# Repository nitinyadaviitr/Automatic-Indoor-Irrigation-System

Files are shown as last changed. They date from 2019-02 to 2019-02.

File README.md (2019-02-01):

# Indoor-Irrigation-System

# Abstract
Our motivation to build this bot is to preserve our green earth and save water by changing the conventional way of plantation.  

# Team Members
<ul>
<li ><a href="https://www.facebook.com/people/Nitin-Yadav/100002014363690">Nitin Yadav</a></li>
<li><a href="https://www.facebook.com/utkarshdeepak23">Utkarsh Deepak</a></li>
<li><a href="https://www.facebook.com/tathagat.chaurasiya">Tathagat Chaurasiya</a></li>
<li><a href="https://www.facebook.com/profile.php?id=100004414771823">Ashish Kumar</a></li>
<li><a href="">Abhishek Mishra</a></li>
<li><a href="https://www.facebook.com/profile.php?id=100011648292342">Rahul Yadav</a></li>
</ul>

# Mentors
<ul>
<li><a href="https://www.facebook.com/profile.php?id=100003364416121">Mohit Gupta</a></li>
<li><a href="https://www.facebook.com/prasants021">Prashant Shekhar Singh</a></li>
<li><a href="https://www.facebook.com/clickonshivam">Shivam Parashar</a></li>
<li><a href="https://www.facebook.com/pritam6505">Pritam Kumar</a></li>
<li><a href="https://www.facebook.com/pankajmindfreak">Pankaj Kumar Singh</a></li>
</ul>

# Pre-Requisites
 
 <b>Hardware:</b>
<ol>
<li>Arduino UNO</li>
<li>2	Motor Driver L298N</li>
<li>12V Solenoidal Value</li>
<li>1 Servo motor MG995</li>
<li>3 High Torque Stepper Motors</li>
<li>ULN2003</li>
<li>12V DC Power Adapter</li>
<li>Relimates</li>
<li>Jumper Wires</li>
<li>LM317T Voltage Divider</li>
<li>Resistors</li>
<li>Breadboard</li>
<li>DST</li>
<li>15cm and 50cm Slider</li>
<li>Wooden Base (dia.52cm)</li>
<li>Wooden Circular Rim(inner dia. 980mm and outer dia. 1080mm)</li>
<li>5m Square Channel</li>
<li>L Channels</li>
<li>Rack And Pinion</li>
<li>Aluminium Plate</li>
<li>Aluminium Sheet</li>
<li>Hollow Circular Rod</li>
<li>Motor Mount</li>
<li>Some 3d printed Parts</li> 
</ol>

 <b>Software:</b>
 
•	<a href ="https://www.arduino.cc/en/main/software">Arduino IDE</a>

# D.I.Y. Steps From Scratch
<ol>
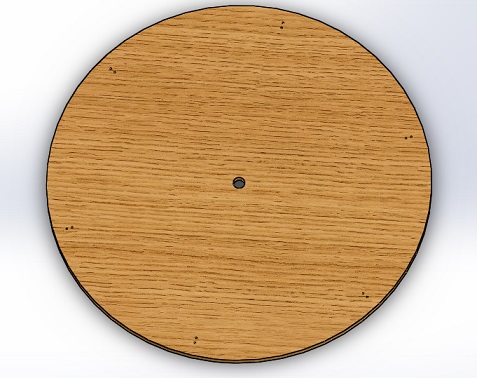
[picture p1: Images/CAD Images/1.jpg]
<li><p>A wooden base of 104cm diameter is chosen as the base for the whole model. A cavity (diameter) is made so that a rod can be placed to support the moving arm.</p></li>
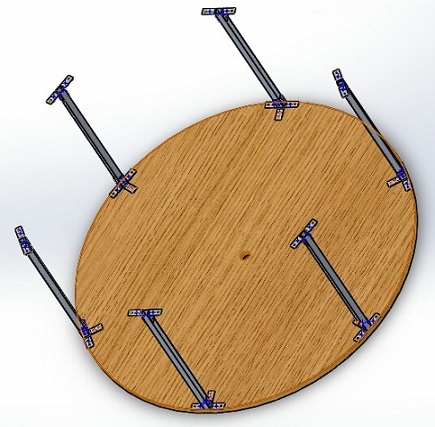
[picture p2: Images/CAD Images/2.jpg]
<li><p>6 square channels of length 50cm are mounted vertically on the wooden base with the help of L-channel to give them a rigid grip on the base. Every square channel has 3 L-channel attached to it on the base and 2 on its top so that the circular rim is fixed firmly and does not move when the arm rotates on it. This is important for a precise movement.</p></li>
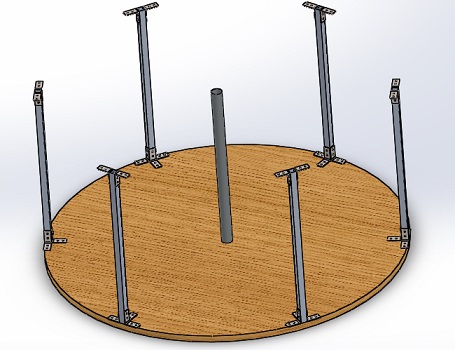
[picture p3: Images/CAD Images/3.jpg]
<li><p>To give support to the moving arm, a rod of 51.4 cm is fixed on the base with a diameter of 3.17cm.</p></li>
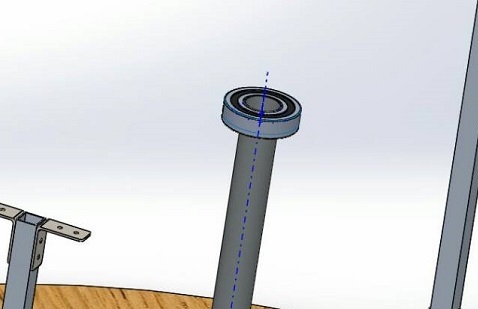
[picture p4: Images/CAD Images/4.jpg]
<li><p>A ball bearing of the same inner diameter as that of the rod is fixed on the rod so that the arm can rotate.</p></li>
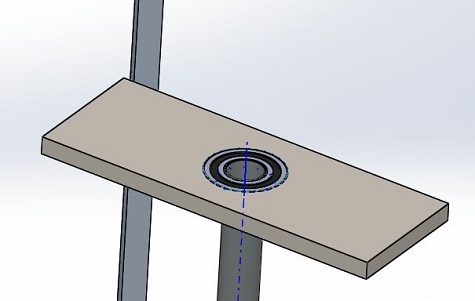
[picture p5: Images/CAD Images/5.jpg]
<li><p>An aluminum plate of about 1cm thickness is used to make a rectangular plate of about 11cm*30 cm, on which, whole of the arm is to be mounted. This aluminum plate has a circular cavity in which the bearing is fitted.</p></li>
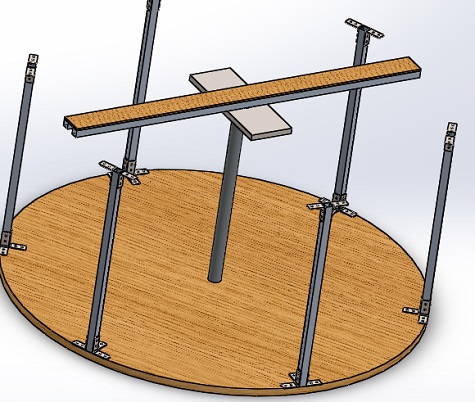
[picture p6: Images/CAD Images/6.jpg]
<li><p>The arm has two square channels of 96cm on which a cardboard sheet is mounted to have a platform for rest of the mechanism.</p></li>
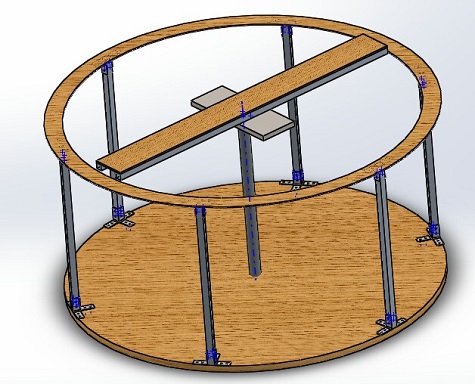
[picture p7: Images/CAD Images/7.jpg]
<li><p>The rim is placed on the vertical square channels and fixed by screwing it to the 2 L-channels.</p></li>
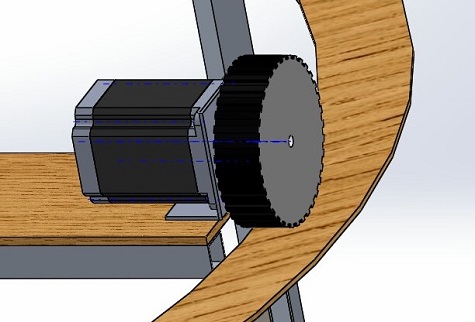
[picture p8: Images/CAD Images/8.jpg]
<li><p>A stepper motor (with a wheel) is fixed at one end of the arm to provide the circular motion to the arm. The motor is mounted on the cardboard sheet with a motor mount.</p></li>
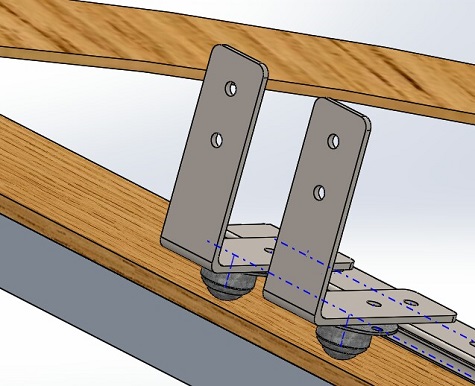
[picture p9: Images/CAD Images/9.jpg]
<li><p>A linear slider of 50cm is screwed on the cardboard sheet for the linear movement of the seeding mechanism. At the end of slider, 2 L-channel are fixed with castor wheels attached at their bottom to provide a smooth movement to the slider despite of the weight of vertical mechanism.</p></li>
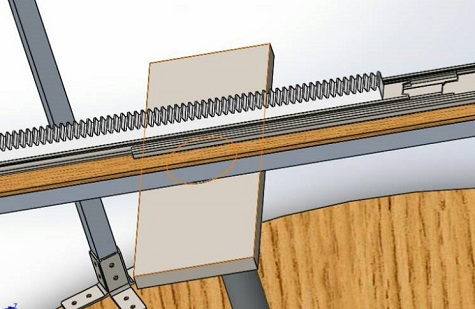
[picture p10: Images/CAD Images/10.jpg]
<li><p>A rack of 40cm is attached on the slider to move it through a stepper motor.</p></li>
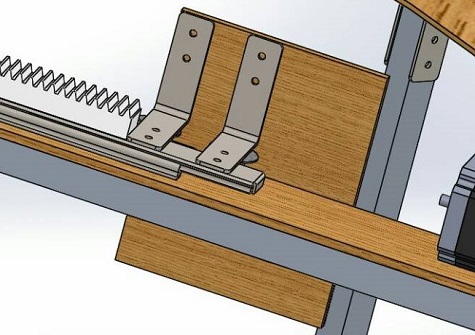
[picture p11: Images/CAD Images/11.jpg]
<li><p>To support the vertical mechanism, a wooden sheet of 15cm*15 cm is used and is fixed on the 2 L-channels with the help of screws.</p></li>
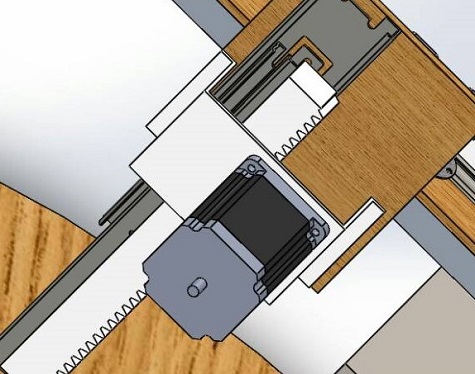
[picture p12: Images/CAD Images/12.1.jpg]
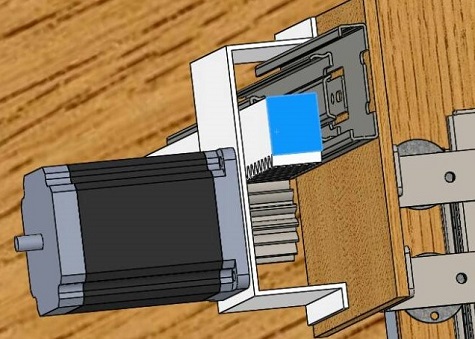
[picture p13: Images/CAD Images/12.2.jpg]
<li><p>In the vertical mechanism, a slider of 15cm is fixed on the wooden sheet and a rack of 25cm is wooden sheet through a u-shaped motor mount (made of ABS/PPS, for 3D printing you can directly access the solid works file provided)</p> </li>
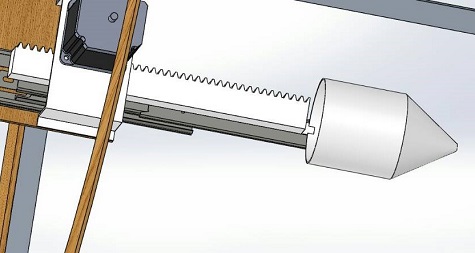
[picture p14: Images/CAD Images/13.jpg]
<li><p>For seeding, a conical flask with a cylindrical top, the seed storage, (made of ABS/PPS) is used in which a servo motor is fixed. The servo motor is used to have a periodic opening and closing of a hole in the storage.</p></li>
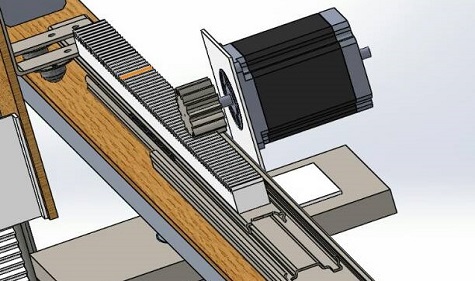
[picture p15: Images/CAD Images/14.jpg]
<li><p>The motor for movement of slider on the horizontal arm is mounted through a motor mount (made of ABS/PPS).</p></li>
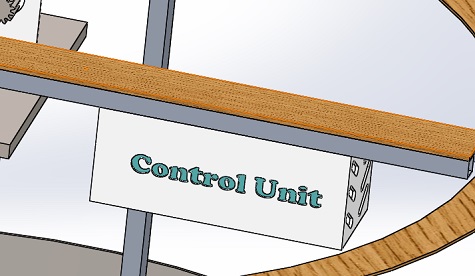
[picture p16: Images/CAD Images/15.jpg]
<li><p>At the vacant side of the arm, whole of the electronic system is mounted. To power the model, the adapter wire is passed through the middle rod. </p></li>
<li>On the aluminum plate in the middle, opposite to the stepper motor, a solenoidal valve is fixed to control the flow of the water.</li>
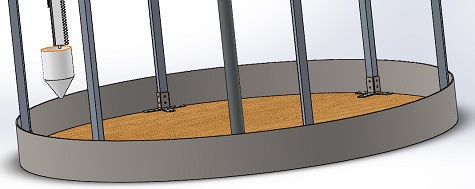
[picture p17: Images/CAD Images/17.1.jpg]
<li><p>Boundary of metal sheet is made to support soil.</p></li>
<li>The water is provided through a container at a certain height higher than the arm to the solenoidal valve.</li>
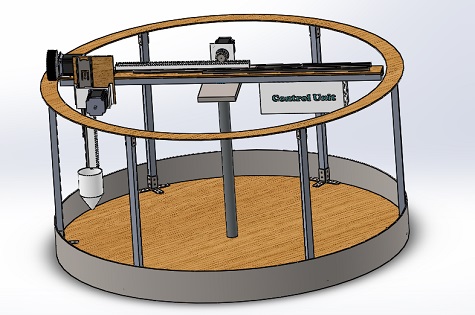
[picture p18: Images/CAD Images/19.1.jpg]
<li><p>After the whole model is made, the whole weight is about 23-25 kg.</p></li>
</ol>

# Instruction on using source code
 Our overall code consists of three sub files. One of them is the <a href="https://github.com/marsiitr/Indoor-Irrigation-System/blob/master/main_code/main_code.ino">main file</a> and others consists of only functions or methods definitons which are called/used in the main file.All the subfiles have been uploaded in github. First, you have to download them all and put them in a folder that has the same name as that of the main file( In our case, "main_code" is the main file).Once you have done this and connected the hardware properly, then you just have to upload the main file to the arduino board and you are ready to go.
# Photos
<div>
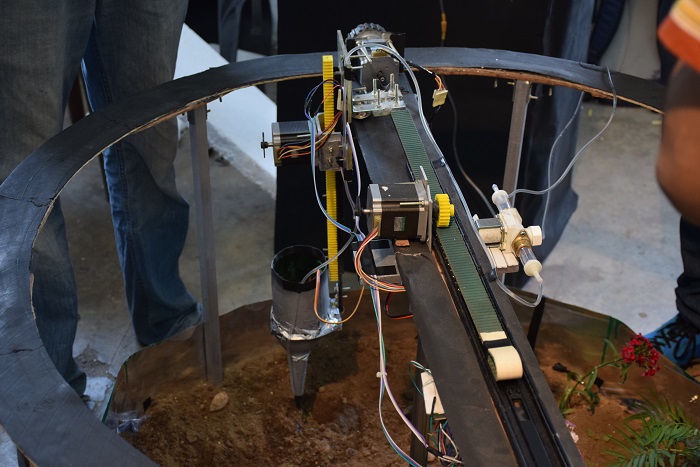
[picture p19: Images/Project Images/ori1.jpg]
<br/>
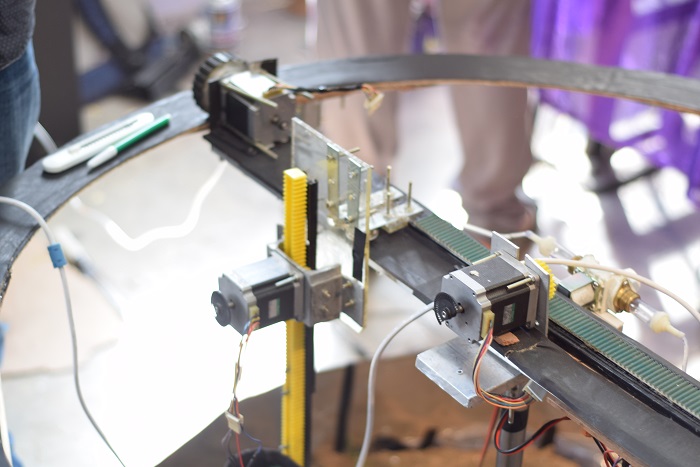
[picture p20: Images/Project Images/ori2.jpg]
<br/>
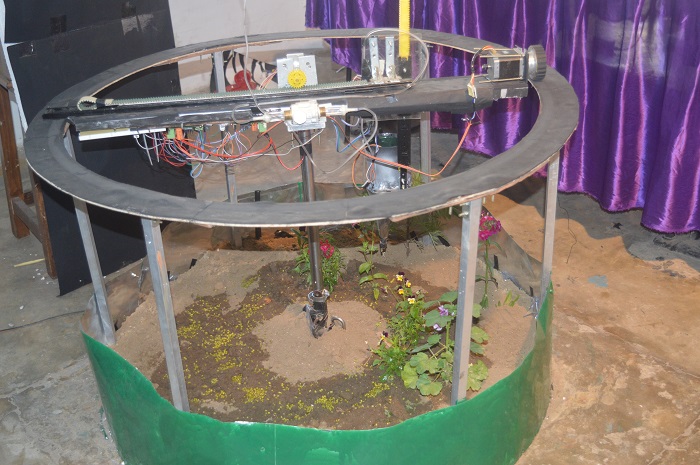
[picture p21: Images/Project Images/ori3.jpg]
<br/>
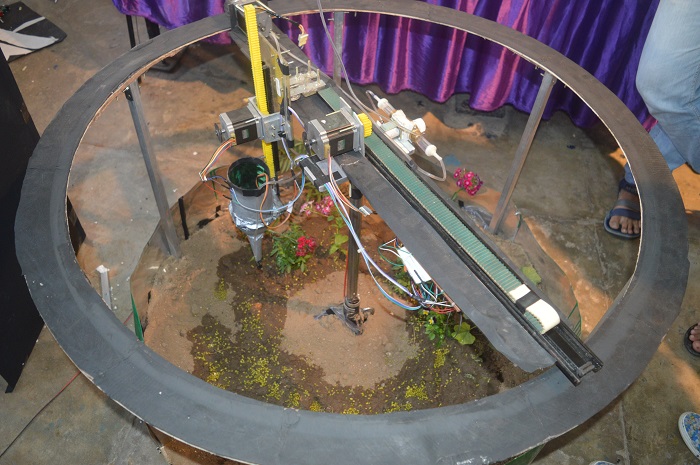
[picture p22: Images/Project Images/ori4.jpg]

</div>

# Results  
1. The mechanism used in the Bot is very effective in saving water and using it efficiently both position and time-wise.
2. The seed bowing mechanism gives us a platform to use the space on the used patch of land efficiently. It can used to accurately place the seed in the position we want to and that is needed to.
3. The energy requirements of the Bot is very low and can be used for long-time with low electricity requirements.
4. The bot has very low heat radiation and thus can be used with continuous working for long time-span.
5. It helps us to grow the plant with proper use of water which results in proper growth of the plant.

# Future scope
 1. This bot has a very good scope in future for people who are not able to give time in gardening but want a patch of land full of   flowers in their backyard. They would require just to spend a few minutes in giving the seeds and water supply to the bot and       rest of the work is automatically done by the bot.
2. For research purposes this bot can be used by researchers to examine the soil quality and its requirements for plantation accurately and without spending much time as most of the work is done by the bot.
3. By farmers to have a proper information about the water and pesticide requirements of soil of their farm so that the growth of grains, vegetables etc. is done with precise information and their growth is properly examined and good quality crops are grown on a larger scale without wastage of water and other resources.

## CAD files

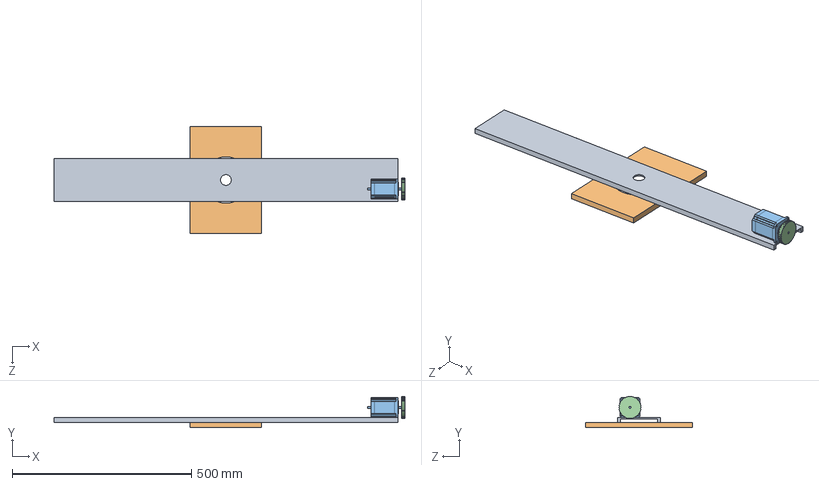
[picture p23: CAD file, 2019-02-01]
Solidworks Assembly/ARM.SLDASM
980.0 x 87.8 x 300.0 mm
arm
holder
step motor

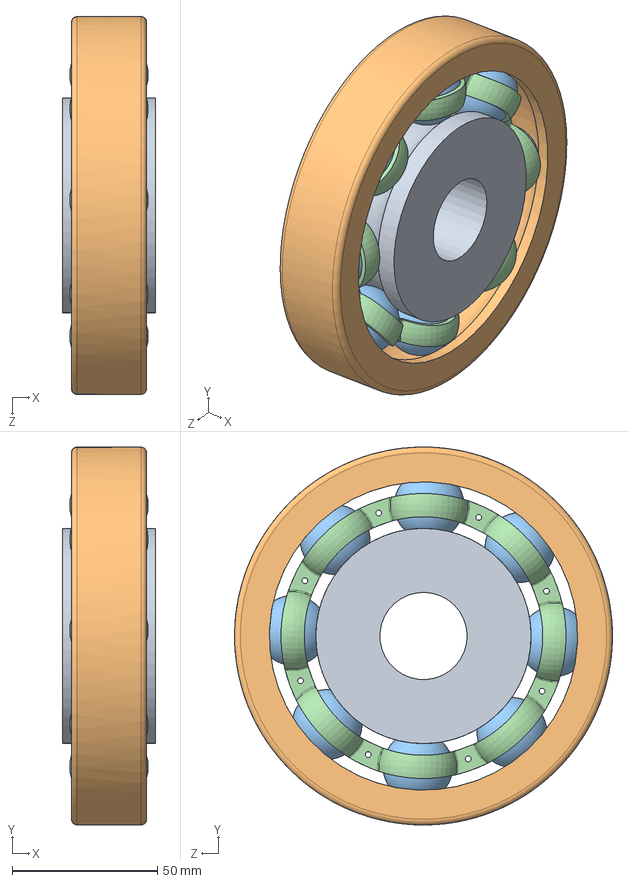
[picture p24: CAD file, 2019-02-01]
Solidworks Assembly/bearing.SLDASM
32.0 x 130.0 x 130.0 mm
hat' x 2

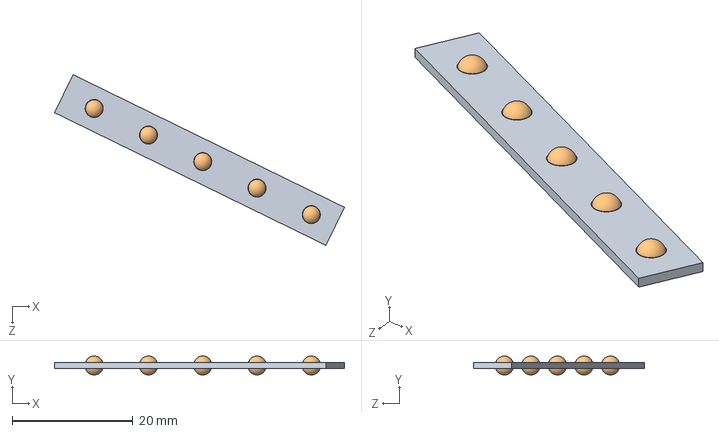
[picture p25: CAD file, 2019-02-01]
Solidworks Assembly/slider 15 cm/MIDDLE SLID WITH BEARING.SLDASM
48.0 x 3.14 x 28.2 mm
middle slit
ball 3 mm x 10

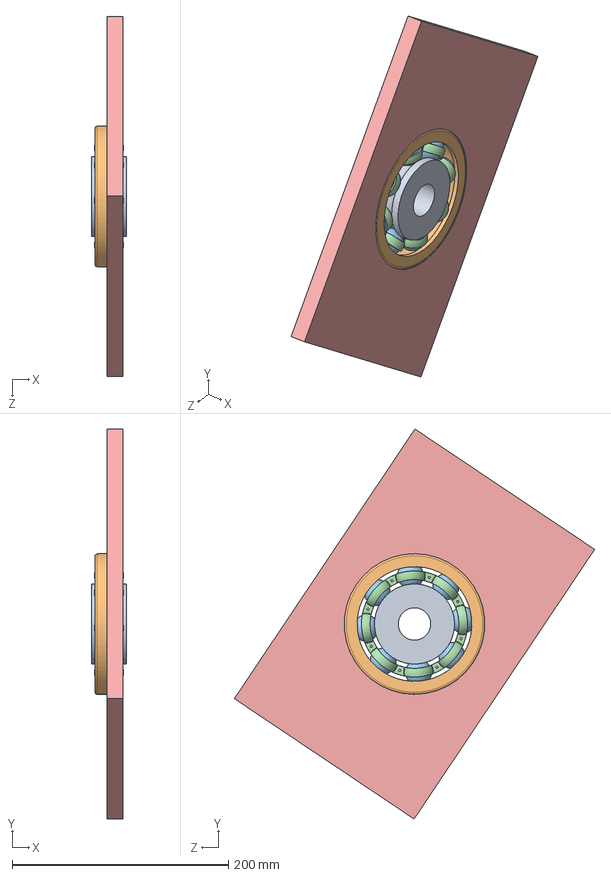
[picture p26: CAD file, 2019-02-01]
Solidworks Assembly/holder1.SLDASM
32.0 x 360.6 x 333.1 mm
hat' x 2
holder

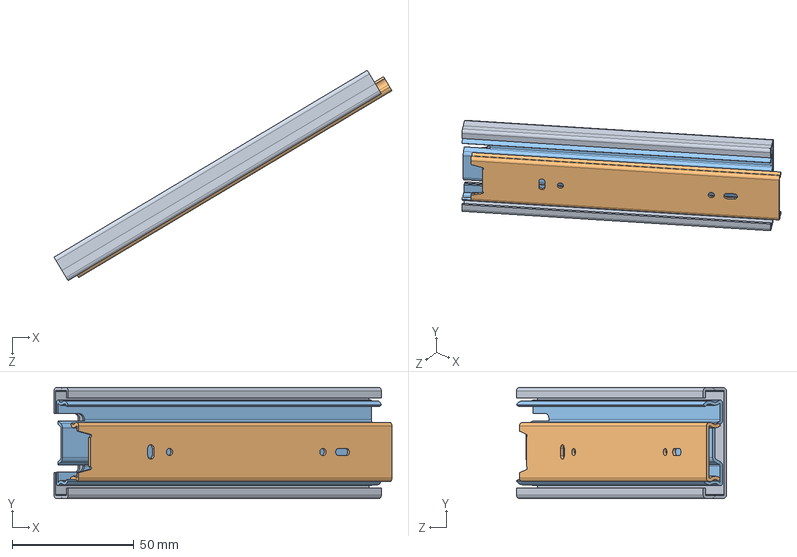
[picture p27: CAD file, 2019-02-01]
Solidworks Assembly/slider 15 cm/final asyy.SLDASM
139.0 x 45.6 x 86.5 mm
base slider final
top slider
Middle slider

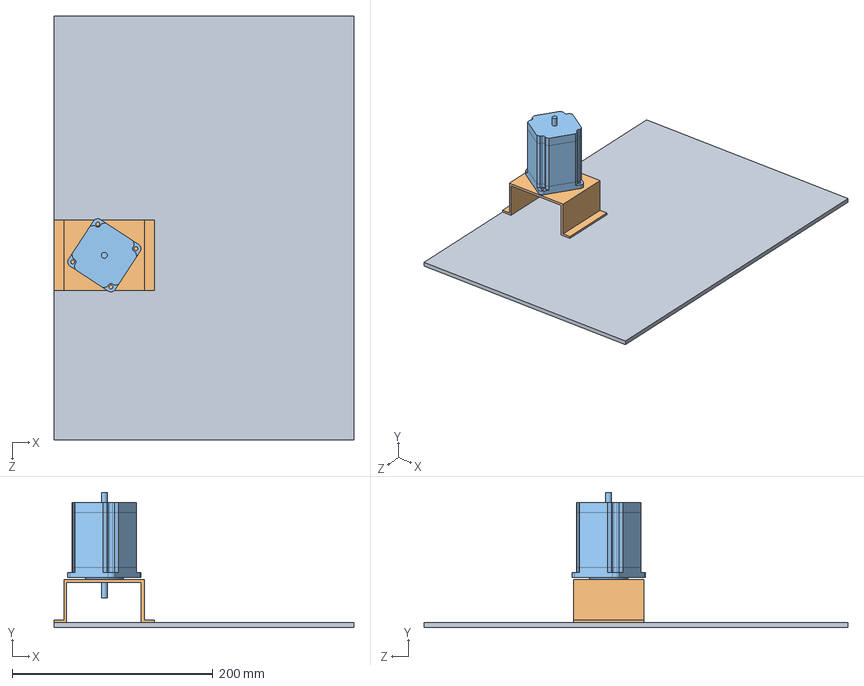
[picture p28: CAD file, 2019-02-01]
Solidworks Assembly/Vertical.SLDASM
298.8 x 134.6 x 422.7 mm
v1
v2
step motor

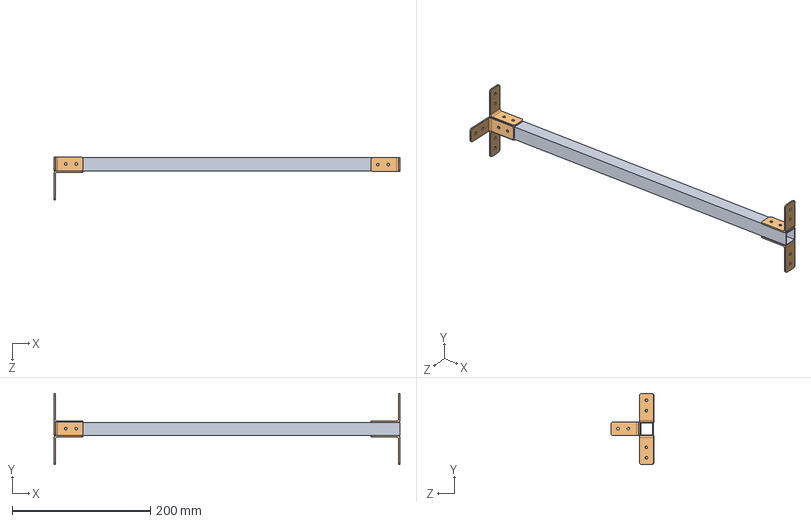
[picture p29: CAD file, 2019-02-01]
Solidworks Assembly/sq_channel_lmount.SLDASM
500.0 x 103.1 x 62.0 mm
Sq_channel
L mount 4mm x 5

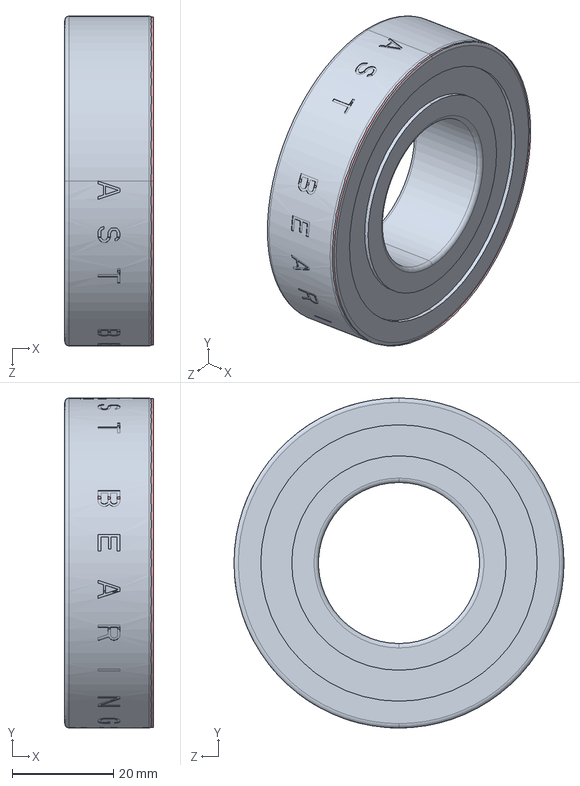
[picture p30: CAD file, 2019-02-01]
Solidworks Assembly/ast ball bearing/AST_Bearings_1657-2RS.SLDASM
17.5 x 65.1 x 65.1 mm
1657-2RS_SOLID_1
1657-2RS_SOLID_2
1657-2RS_SOLID_3
1657-2RS_SOLID_4
1657-2RS_SOLID_5
1657-2RS_SOLID_6
1657-2RS_SOLID_7
1657-2RS_SOLID_8
1657-2RS_SOLID_9
1657-2RS_SOLID_10
1657-2RS_SOLID_11
1657-2RS_SOLID_12
1657-2RS_QUILT_1

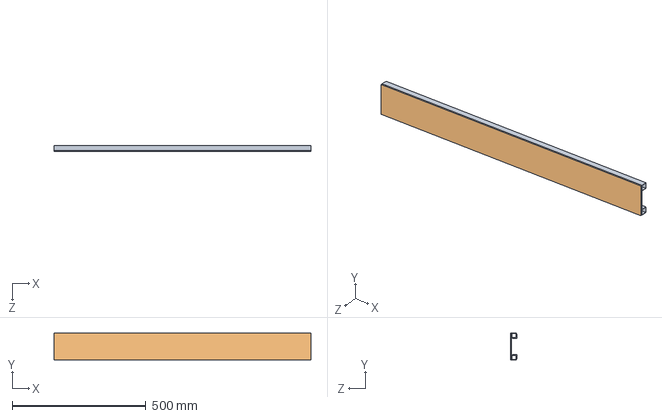
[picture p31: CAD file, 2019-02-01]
Solidworks Assembly/horizontal arm.SLDASM
960.0 x 100.0 x 24.0 mm
Sq_channel arm x 2
horizontal arm base

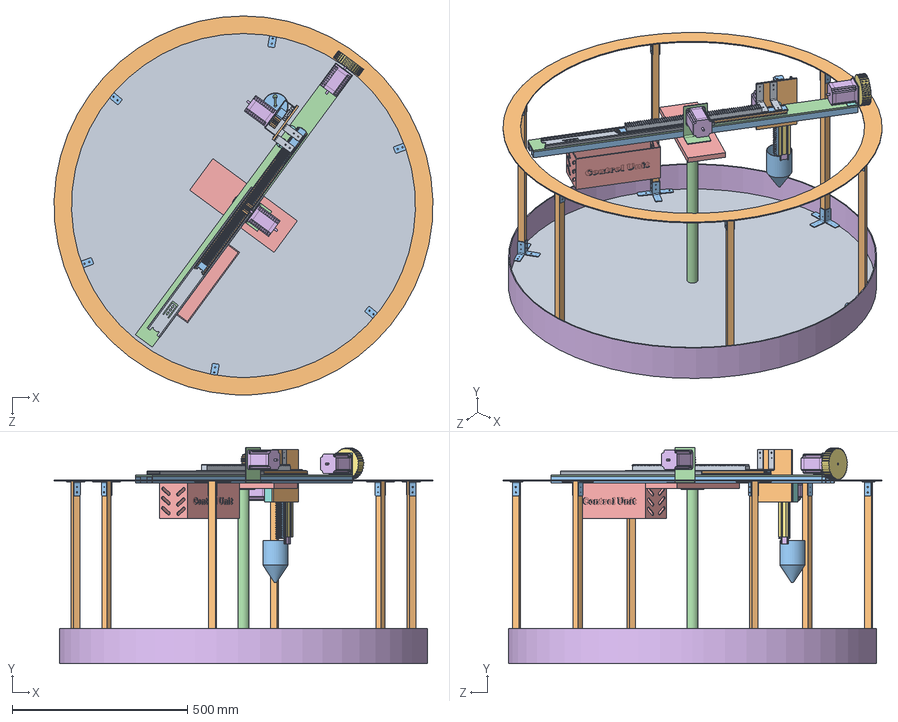
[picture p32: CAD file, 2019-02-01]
Solidworks Assembly/Main assembly.SLDASM
1079.5 x 616.0 x 1080.0 mm
base plate
Sq_channel x 6
L mount 4mm x 30
centre_rod
1657-2RS_SOLID_1
1657-2RS_SOLID_2
1657-2RS_SOLID_3
1657-2RS_SOLID_4
1657-2RS_SOLID_5
1657-2RS_SOLID_6
1657-2RS_SOLID_7
1657-2RS_SOLID_8
1657-2RS_SOLID_9
1657-2RS_SOLID_10
1657-2RS_SOLID_11
1657-2RS_SOLID_12
1657-2RS_QUILT_1
rim
Sq_channel arm x 2
horizontal arm base
holder
step motor x 3
wheel
horizontal stepper mount
Base
Middle
Top
Bearing BM-T
Bearing BM-B
Bearing MT-T
Bearing MT-B
ball castor x 2
L mount 4mm - Copy x 2
vertical base
servo horn
base slider final
top slider
Middle slider
vertical motor mounting
rack 40cm
Pinion x 2
rack 25cm
horizontal_stepper_mount
control box
bound

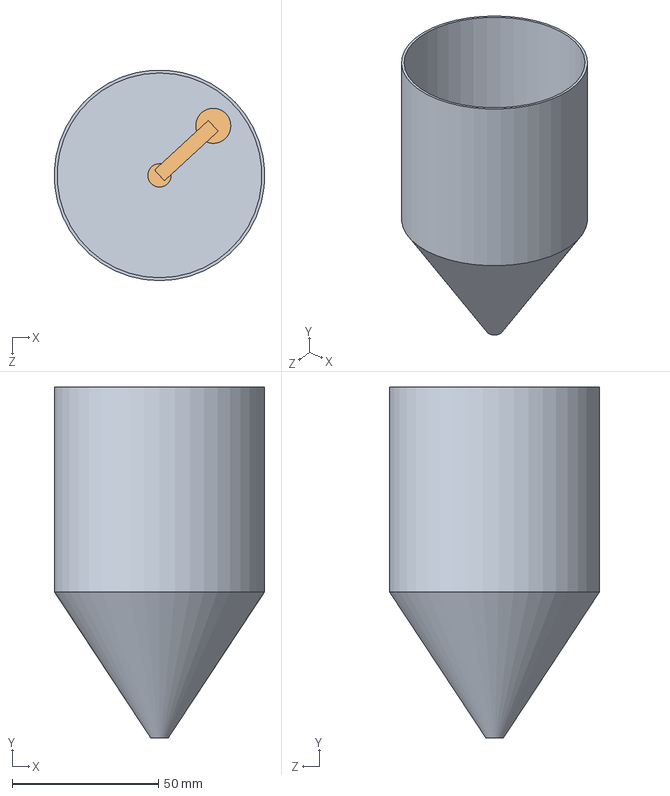
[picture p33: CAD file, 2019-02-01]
Solidworks Assembly/sowing mech.SLDASM
72.0 x 120.0 x 71.9 mm
servo horn

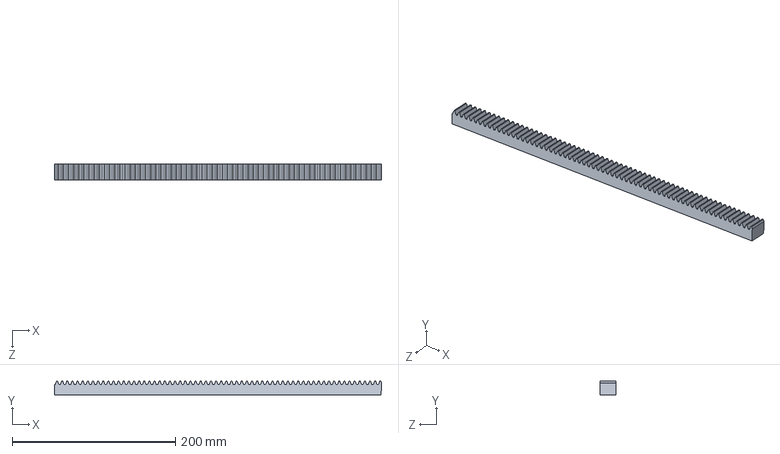
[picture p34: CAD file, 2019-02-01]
Solidworks Assembly/rack and pinion/rack 40cm.sldprt
400.4 x 17.0 x 20.0 mm

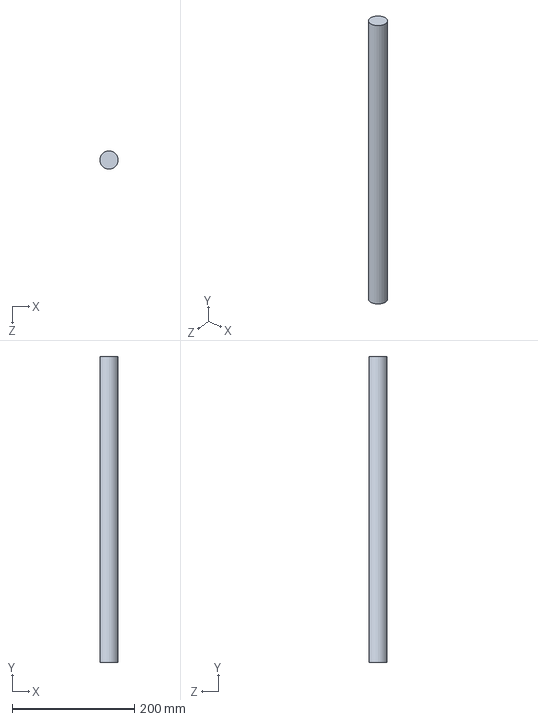
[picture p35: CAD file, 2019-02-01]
Solidworks Assembly/rod.SLDPRT
30.0 x 500.0 x 30.0 mm

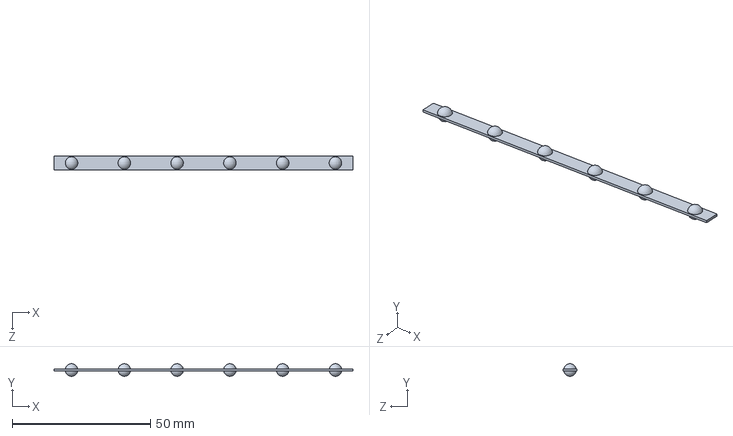
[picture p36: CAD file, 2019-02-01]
Solidworks Assembly/slide 50 cm/Bearing MT-B.sldprt
107.9 x 4.52 x 5.08 mm

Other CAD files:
Solidworks Assembly/ast ball bearing/1657-2RS_QUILT_1.sldprt
Solidworks Assembly/slider 15 cm/middle slit.SLDPRT
Solidworks Assembly/stepper motor/Renderings/step motor.SLDPRT
Solidworks Assembly/stepper motor/step motor.SLDPRT
Solidworks Assembly/L mount 4mm - Copy.SLDPRT
Solidworks Assembly/L mount 4mm.SLDPRT
Solidworks Assembly/Pinion.SLDPRT
Solidworks Assembly/Sq_channel arm.SLDPRT
Solidworks Assembly/Sq_channel.SLDPRT
Solidworks Assembly/arm.SLDPRT
Solidworks Assembly/ast ball bearing/1657-2RS_SOLID_1.sldprt
Solidworks Assembly/ast ball bearing/1657-2RS_SOLID_10.sldprt
Solidworks Assembly/ast ball bearing/1657-2RS_SOLID_11.sldprt
Solidworks Assembly/ast ball bearing/1657-2RS_SOLID_12.sldprt
Solidworks Assembly/ast ball bearing/1657-2RS_SOLID_13.sldprt
Solidworks Assembly/ast ball bearing/1657-2RS_SOLID_2.sldprt
Solidworks Assembly/ast ball bearing/1657-2RS_SOLID_3.sldprt
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

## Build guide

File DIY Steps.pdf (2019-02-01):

1. A wooden base of 104cm diameter is chosen as the base for the whole model. A cavity (diameter) is made so that a rod can be placed to support the moving arm.

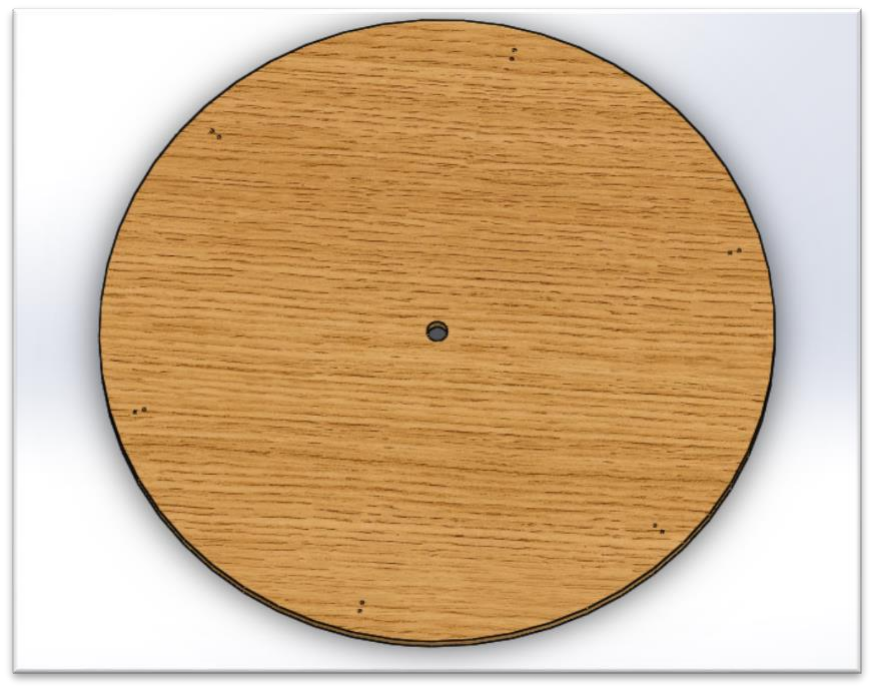
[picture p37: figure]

2.6 square channels of length 50cm are mounted vertically on the wooden base with the help of L-channel to give them a rigid grip on the base. Every square channel has 3 L-channel attached to it on the base and 2 on its top so that the circular rim is fixed firmly and does not move when the arm rotates on it. This is important for a precise movement.

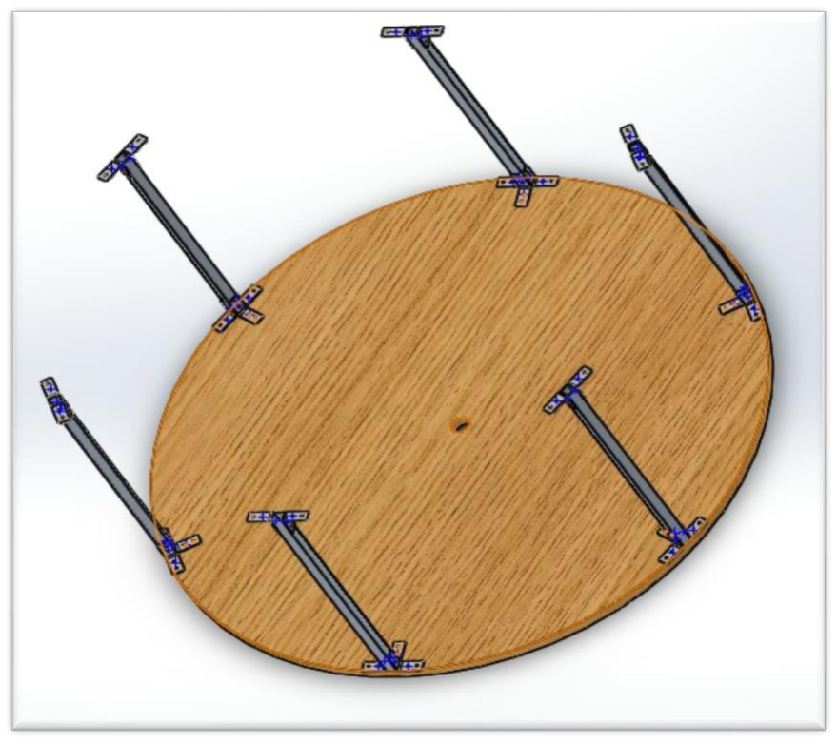
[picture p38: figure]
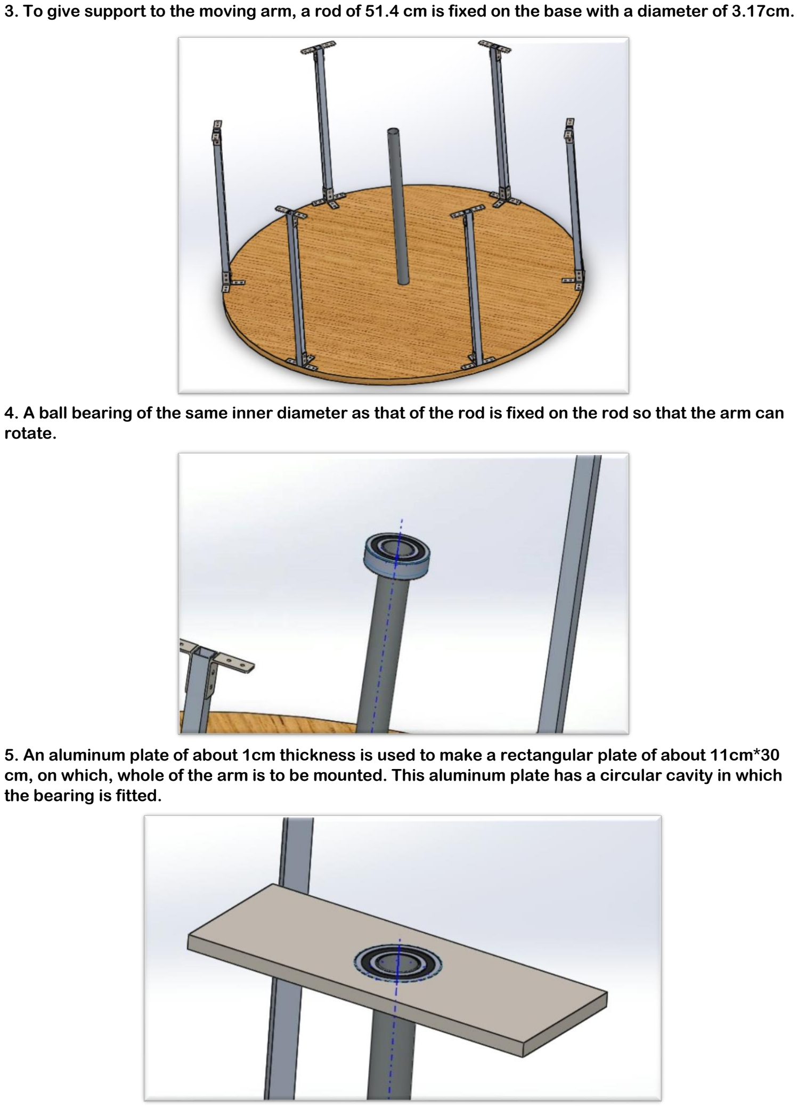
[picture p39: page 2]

3. To give support to the moving arm, a rod of 51.4 cm is fixed on the base with a diameter of 3.17cm.
4. A ball bearing of the same inner diameter as that of the rod is fixed on the rod so that the arm can rotate.
5. An aluminum plate of about 1cm thickness is used to make a rectangular plate of about 11cm*30 cm, on which, whole of the arm is to be mounted. This aluminum plate has a circular cavity in which the bearing is fitted.

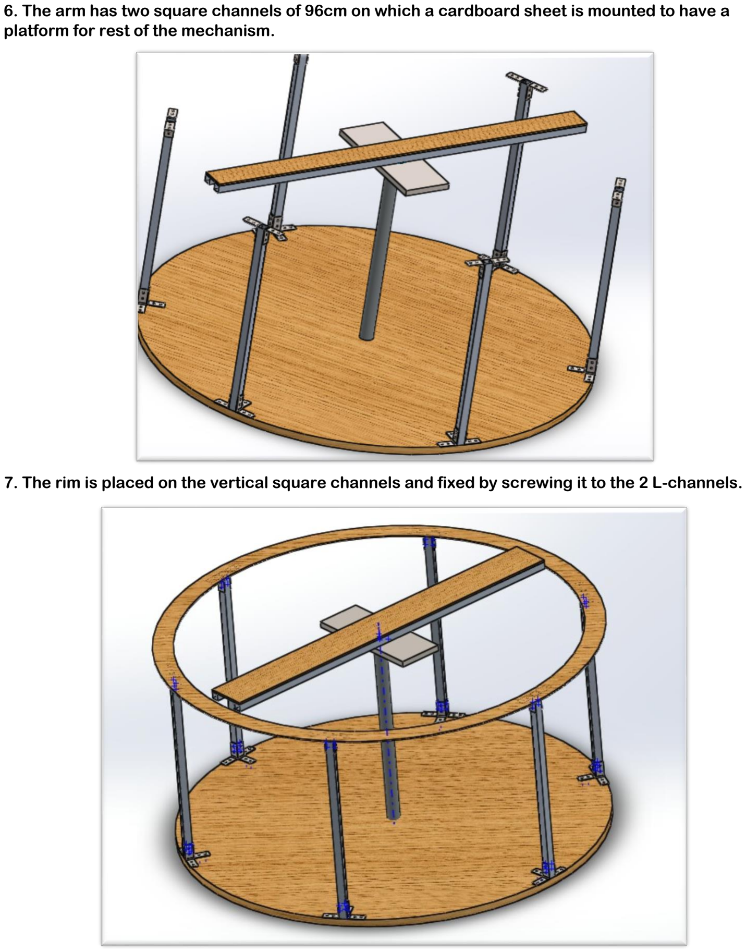
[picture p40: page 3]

6. The arm has two square channels of 96cm on which a cardboard sheet is mounted to have a platform for rest of the mechanism.
7. The rim is placed on the vertical square channels and fixed by screwing it to the 2 L-channels.

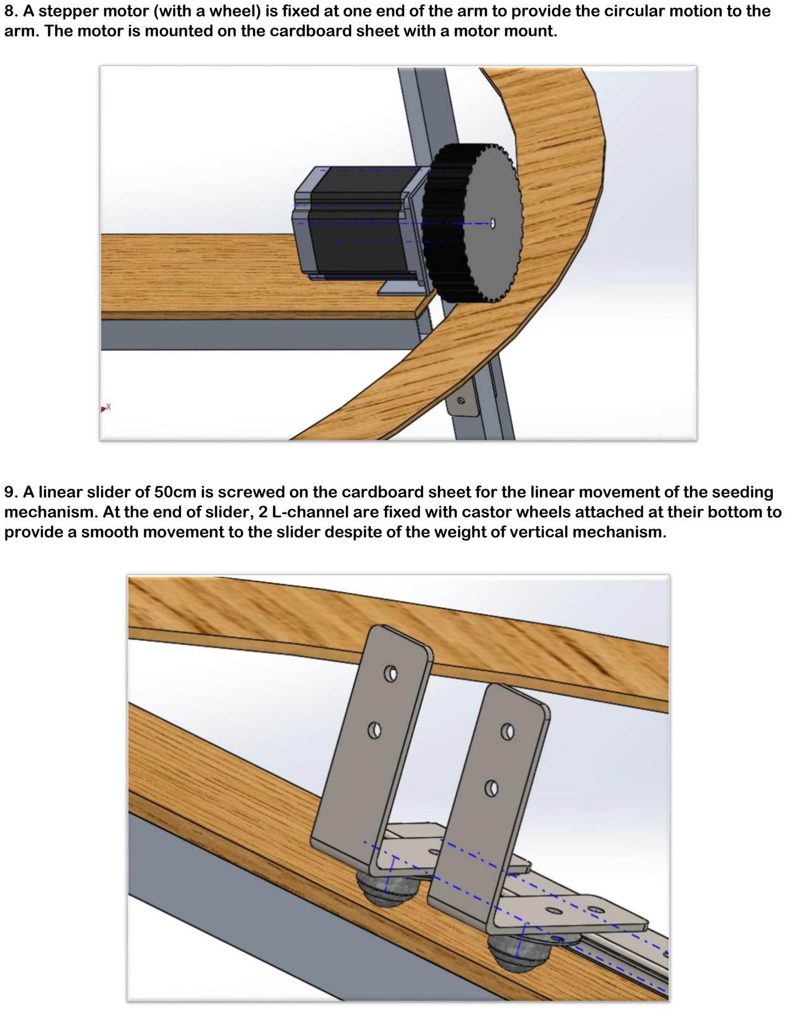
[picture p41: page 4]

8. A stepper motor (with a wheel) is fixed at one end of the arm to provide the circular motion to the arm. The motor is mounted on the cardboard sheet with a motor mount.
9. A linear slider of 50cm is screwed on the cardboard sheet for the linear movement of the seeding mechanism. At the end of slider, 2 L-channel are fixed with castor wheels attached at their bottom to provide a smooth movement to the slider despite of the weight of vertical mechanism.

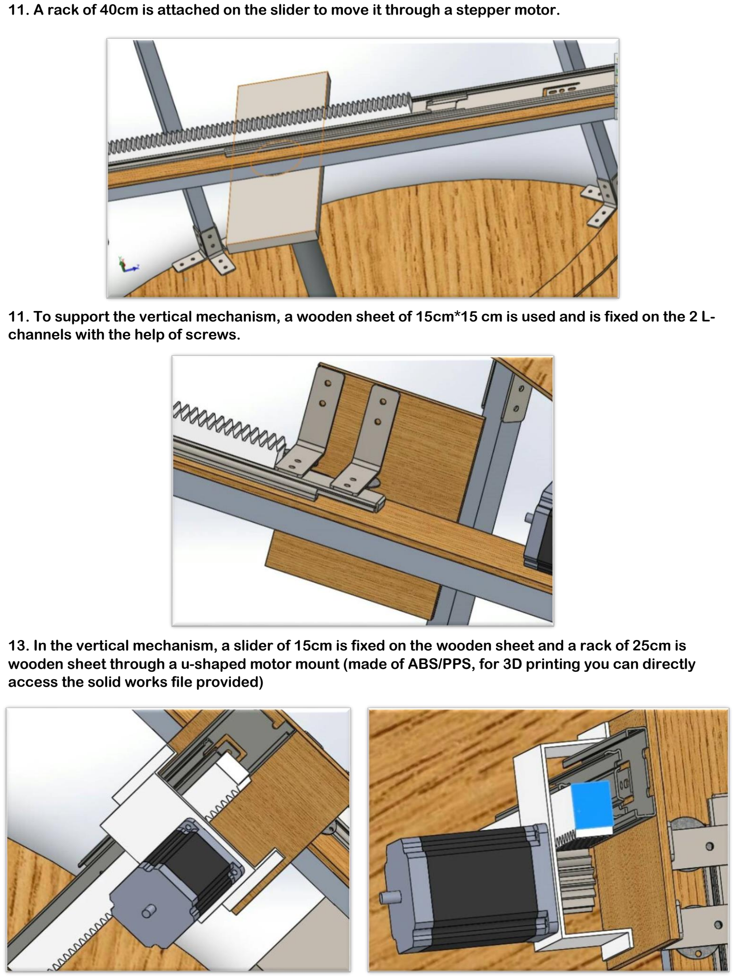
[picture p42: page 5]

11. A rack of 40cm is attached on the slider to move it through a stepper motor.
11. To support the vertical mechanism, a wooden sheet of 15cm*15 cm is used and is fixed on the 2 L-channels with the help of screws.
13. In the vertical mechanism, a slider of 15cm is fixed on the wooden sheet and a rack of 25cm is wooden sheet through a u-shaped motor mount (made of ABS/PPS, for 3D printing you can directly access the solid works file provided)

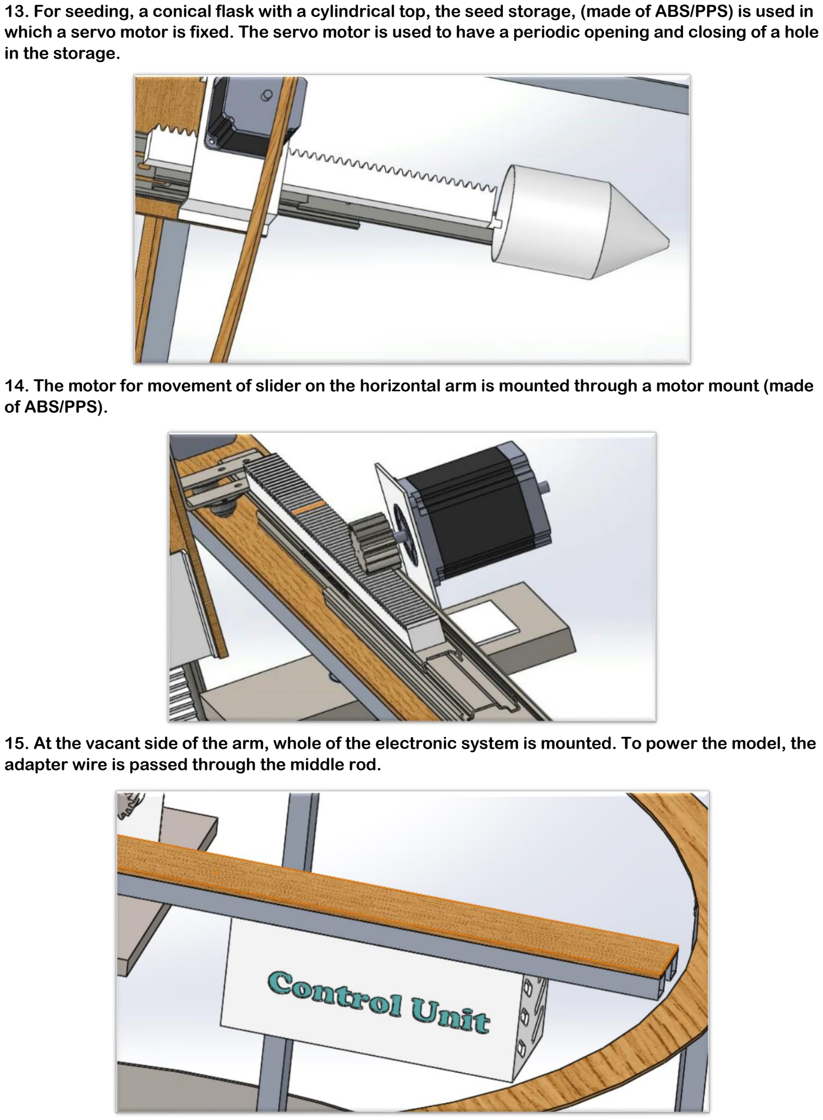
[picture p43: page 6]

13. For seeding, a conical flask with a cylindrical top, the seed storage, (made of ABS/PPS) is used in which a servo motor is fixed. The servo motor is used to have a periodic opening and closing of a hole in the storage.
14. The motor for movement of slider on the horizontal arm is mounted through a motor mount (made of ABS/PPS).
15. At the vacant side of the arm, whole of the electronic system is mounted. To power the model, the adapter wire is passed through the middle rod.

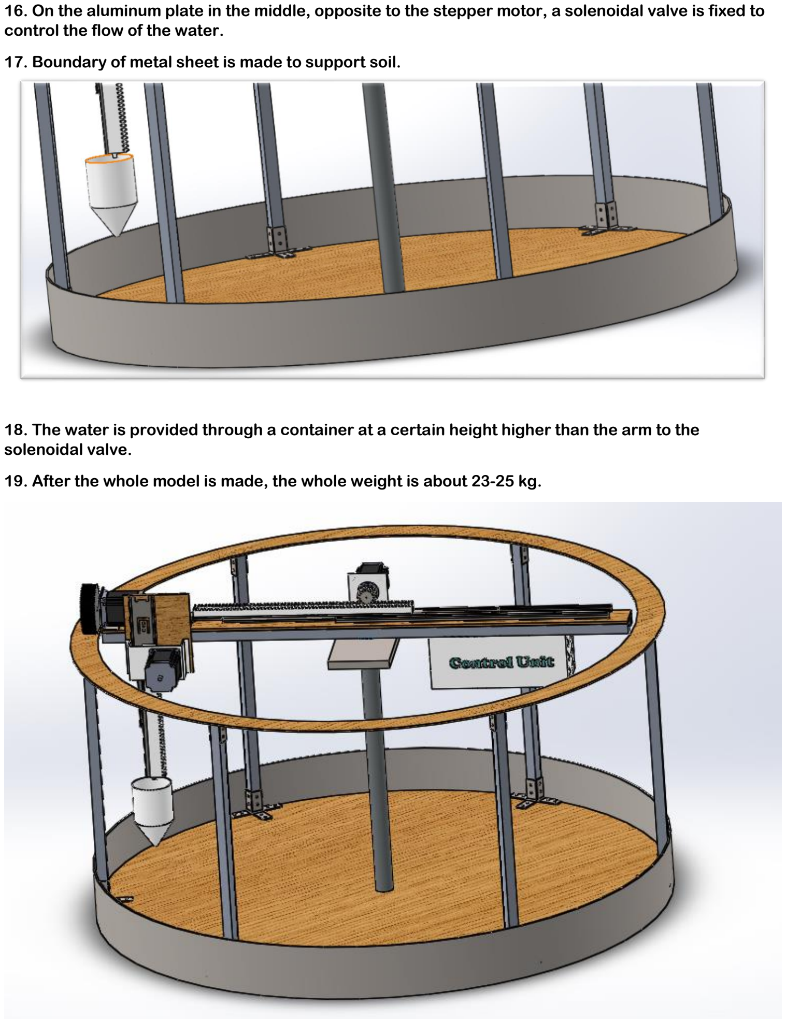
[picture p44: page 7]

16. On the aluminum plate in the middle, opposite to the stepper motor, a solenoidal valve is fixed to control the flow of the water.
17. Boundary of metal sheet is made to support soil.
18. The water is provided through a container at a certain height higher than the arm to the solenoidal valve.
19. After the whole model is made, the whole weight is about 23-25 kg.

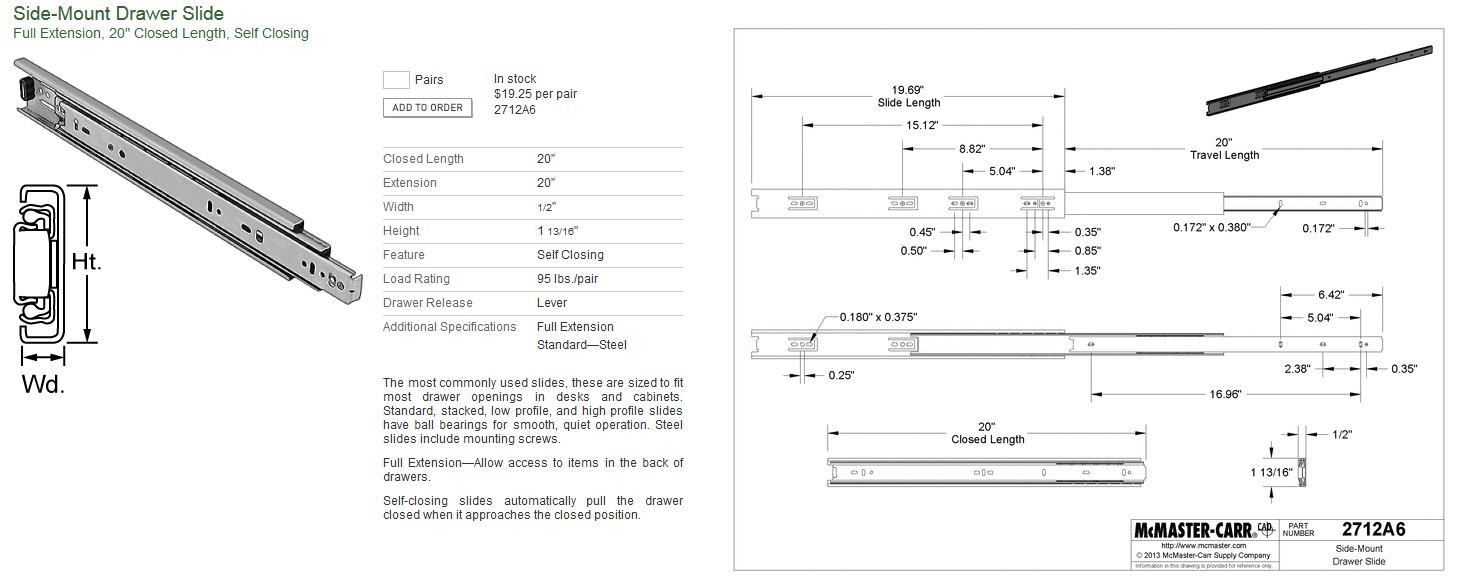
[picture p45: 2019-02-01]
Solidworks Assembly/slide 50 cm/Renderings/Drawer Slide Side-Mount - MMC 2712A6.png

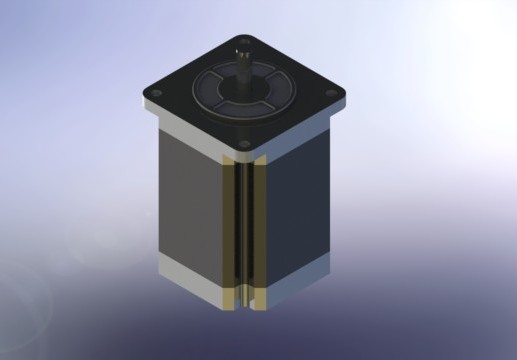
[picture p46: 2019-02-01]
Solidworks Assembly/stepper motor/Renderings/steppermotor.JPG

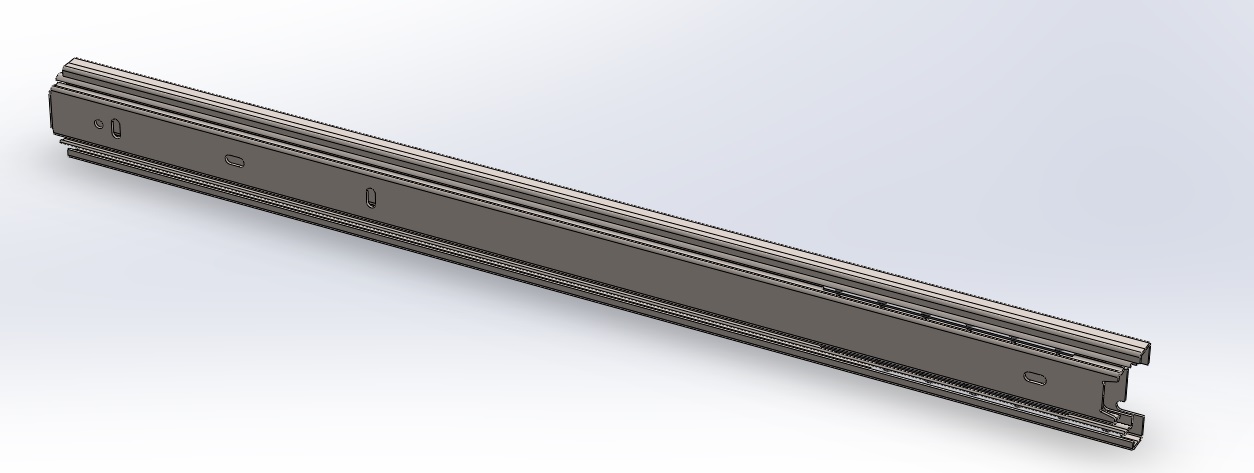
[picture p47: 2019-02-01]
Solidworks Assembly/slide 50 cm/Drawer Slide Side-Mount - Closed.jpg

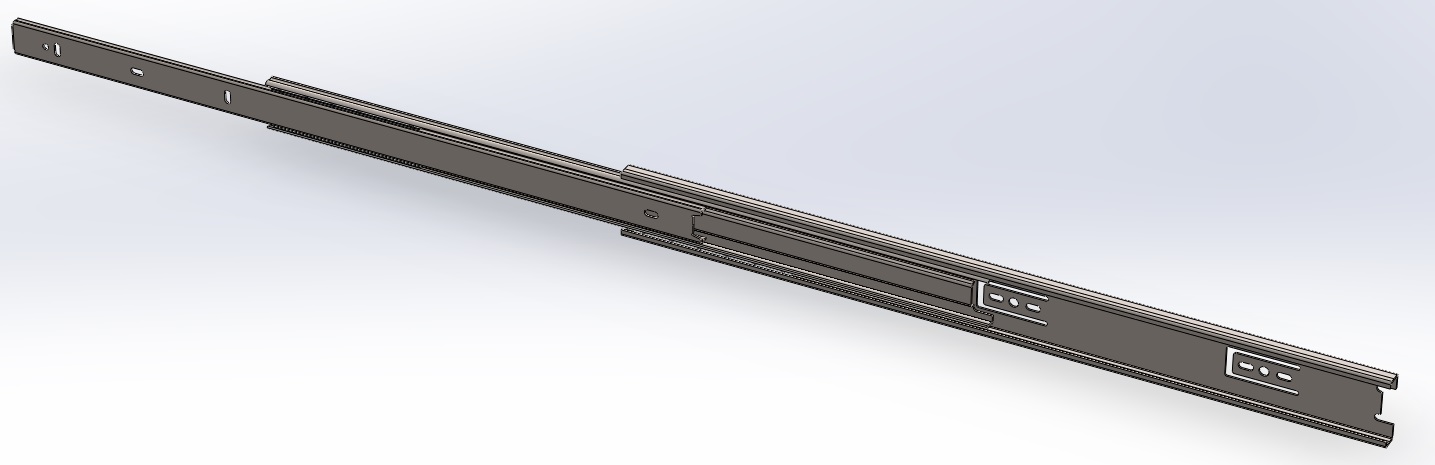
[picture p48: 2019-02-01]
Solidworks Assembly/slide 50 cm/Drawer Slide Side-Mount - Open.jpg

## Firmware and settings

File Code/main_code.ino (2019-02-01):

#include <Stepper.h>
#include <Servo.h>

//#define water 7
int pwm_1 = 9;              
int pwm_2 = 5;
int pwm_3 = A1;
int water =7;           //For Solenoidal valve
int count = 0;
int steps = 200;
int pos = 120; 
const int stepsPerRevolution = 200;
Stepper myStepper1(stepsPerRevolution, 10, 11, 12, 13);//For horizontal movement
Stepper myStepper2(stepsPerRevolution, 8, 2, 3, 4);//For circular movement
Stepper myStepper3(stepsPerRevolution, A2, A3, A4, A5);//For vertical movement
void seedside();
void irrigateside();
void insert_seed();
void pour();
Servo myservo;
void setup() {
  myStepper1.setSpeed(60);
  myStepper2.setSpeed(60);
  myStepper3.setSpeed(60);
    
analogWrite(pwm_1,0);
  myStepper1.step(100);
  analogWrite(pwm_1, 255); 
  myservo.attach(6); 
    Serial.begin(9600);
  myservo.write(120);

  pinMode(pwm_1, OUTPUT);
  pinMode(pwm_2, OUTPUT);
  pinMode(water, OUTPUT);

}

int counter = 0;
void loop() {  
counter++;
if(counter<5)                   //both sow seed and pour water it in half side of land
{
seedside();
}
else if(counter<9)              //only pour water in the another half side of land
{
irrigateside();
}
else                            //To bring arm back to its initial position
{
  counter = 0;
analogWrite(pwm_2,0);
  myStepper2.step(-2680);
  analogWrite(pwm_2, 255);}
}

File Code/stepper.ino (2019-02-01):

void insert_seed()
{
  analogWrite(pwm_3,0);       
  myStepper3.step(-300); //move the sowing arm down
  analogWrite(pwm_3, 255);
  myservo.write(150);    //open the seed valve
  delay(10);
  analogWrite(pwm_3,0);
  myStepper3.step(+10);  //to shake the sowing arm 
  analogWrite(pwm_3, 255);
  delay(10);
  analogWrite(pwm_3,0);
  myStepper3.step(-10);
  analogWrite(pwm_3, 255);  
  delay(10);
  analogWrite(pwm_3,0);
  myStepper3.step(10);
  analogWrite(pwm_3, 255);
  delay(10);
  analogWrite(pwm_3,0);
  myStepper3.step(-10);
  analogWrite(pwm_3, 255);
  myservo.write(120);
  delay(20);  
  digitalWrite(water,HIGH);   //turn on the solenoidal valve
  delay(2000);
  digitalWrite(water,LOW);    //turn off the solenoidal value
  analogWrite(pwm_3,0);
  myStepper3.step(300);
  analogWrite(pwm_3, 255);
}
void pour()
{
  digitalWrite(water,HIGH);
  delay(1500);
  digitalWrite(water,LOW);
}
void rotate_clock(int n)    // to rotate the horizontal arm in clockwise direction 
{
  analogWrite(pwm_1,0);
  myStepper1.step(n);
  analogWrite(pwm_1, 255);
}
void anti_rotate_clock(int n)  // to rotate the horizontal arm in clockwise direction 
{
  analogWrite(pwm_1,0);
  myStepper1.step(-n);
  analogWrite(pwm_1, 255);
}
